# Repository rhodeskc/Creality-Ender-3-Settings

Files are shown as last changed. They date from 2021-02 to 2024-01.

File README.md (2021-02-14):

# Creality-Ender-3-Marlin-v20x-Firmware-Settings
Marlin settings for my Ender 3.

It has the Gulfcoast Robotics heated bed installed, so the temp sensor bed needed to be updated.  In addition to this, I swapped out the board for the 4.2.7 Silent board.

## Creality-Ender-3-board-v4.2.7
Marlin Firmware to get Creality v4.2.7 boards working

Download bugfix from git hub https://github.com/MarlinFirmware/Marlin/archive/bugfix-2.0.x.zip

Download Configuration exemples: https://github.com/MarlinFirmware/Configurations/archive/bugfix-2.0.x.zip

Editing the configuration and building it in Visual Studio Code:
http://813studios.com/creality-4-2-7-marlin-bltouch-install-notes-ender-3/

Instructions on updating and installing the Gulfcoats heated bed: https://letsprint3d.net/how-to-install-the-gulfcoast-robotics-heated-bed-ender-3-5/
* NEW: #define TEMP_SENSOR_BED 11
* OLD: #define TEMP_SENSOR_BED 1

Copy the \_Bootscreen.h and \_Statusscreen.h files to the Marlin\ folder, the same one that has Marlin.ino in it.

## In platformio.ini
* Change:   default_envs = mega2560\
* To:       default_envs = STM32F103RET6_creality

## Compile

In Auto Build Marlin at Visual Studio, click on Build botton and wait for the green line

## Where is the firmware I've compilled
In my case: $\.pio\build\STM32F103RET6_creality\
File to copy to a SD card to flash the firmware: **$\.pio\build\STM32F103RET6_creality\\\*.bin**

## Originally adapted from:
https://github.com/Flawioo/Creality-Ender-3-board-v4.2.7/blob/master/README.md

----

Copied from: http://813studios.com/creality-4-2-7-marlin-bltouch-install-notes-ender-3/

# Creality 4.2.7 Marlin + BLTouch Install notes (Ender-3)

I ordered an upgraded creality v1.1.5 mainboard off Amazon and was shipped Creality’s latest “silent motherboard” version v4.2.7. The product on amazon was described to have a bootloader flashed directly out of box which would make uploading sketches to the board even easier. I spent hours on Arduino IDE trying to upload with the Sanguino board to no avail. 

**Turns out that the new motherboards use the SD card to flash new firmware. All you need to do is drop the “.bin” file to the root directory.**

This made me realize that I just needed to use Visual Studio Code + Auto Build Marlin to compile and update the printer. If you don’t know how to do that, don’t worry– I got you.

Most of this information was found here, these guys got everything working and were able to put together this helpful document that lays out all of the pin data we have so far for the 4.2.7

## Instructions:
Open up VSC and install Auto Build Marlin plugin.

Once you have those both installed, its time to download and open the firmware for the printer inside of Visual Studio Code. 

### Marlin Configuration
First, download the Marlin 2.X.X bugfix from Github here: https://github.com/MarlinFirmware/Marlin/tree/bugfix-2.0.x

Once that’s downloaded, the next step is to open the “Marlin” **folder** that is found inside of the 2.X.X parent directory.

Once you have that opened, now its time to edit the Marlin config files. Below are the changes that I needed make to get my printer working. Take note that this might not necessarily represent your printers setup. 

* Platform.ini
* Configuration.h
* *(optional) Configuration_adv.h*

### Uploading Firmware to the Printer
Once you’ve made all of the changes listed above, compile the firmware with VSC using the Auto Build Marlin plugin and upload it to the root dir of your SD card. Pop the SD card into your printer and boot it up!

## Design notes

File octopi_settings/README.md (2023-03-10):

# Installation Instructions
1. [Install Pi imager for windows](https://www.raspberrypi.com/software/)
1. Run the installer.
1. Configure it per the instructions [here](https://octoprint.org/download/).
1. Open advanced options by clicking on the button with the gear, or by using the keyboard shortcut ctrl+shift+x
> Specific settings used are:
> - OS =  "Choose OS" > "Other Specific Purpose OS" > "3D printing" > "OctoPi" > "stable" version.
> - SSID / WiFi stuff
> - Change password only
1. Click save
1. Flash the card.
1. Install the card back into the Raspberry Pi and let it boot up.
1. Verify by going to [router main settings](http://192.168.1.1) that it has connected to the network
1. Install the following 3rd party plugins
> - [Automatic Shutdown](https://www.reddit.com/r/octoprint/comments/mm9cbi/automatic_shutdown_after_prints/)
> > Got it working. Installed the plugin shutdown printer https://github.com/devildant/OctoPrint-ShutdownPrinter and set that at 110 degrees and at "Extra command / script" put the line "sudo shutdown -h now". Now the rpi turns off at 110 degrees and turns off the relay connected to the printer.
> - [DisplayLayerProgress](https://all3dp.com/2/must-have-octoprint-plugins/)
> - **Do not install ArcWelder**. See notes under [Cura](#Cura).

OctoPi settings were saved at last install. They can be uploaded from *octoprint-backup-latest.zip*

Once that has completed, set the printer profile settings as follows:
> - **Form factor:** Rectangular
> - **Origin:** Lower Left
> - **Heated Bed:** Yes (checked)
> - **Heated Chamber:** No (unchecked)
> - **Width:** 220mm
> - **Depth:** 220mm
> - **Height:** 250mm
> - **Axes:** Default**
> - **Custom Bounding Box:** No (unchecked)
> - **Nozzle Diameter:** 0.4mm
> - **Number of Extruders:** 1

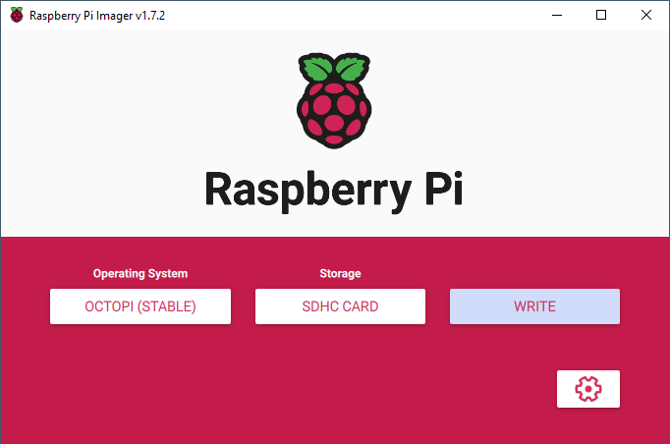
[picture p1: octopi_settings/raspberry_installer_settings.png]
Raspberry Pi settings


## Calibration scripts
1. Create a folder called Calibration
1. Upload calibration scripts from the *\calibration_scripts* directory 

## Cura
1. Install ArcWelder in Cura, but NOT in OctoPrint. It generates a bunch of additional files that are not helpful when you do the OctoPi one.
1. Also install TabAntiWarping extension

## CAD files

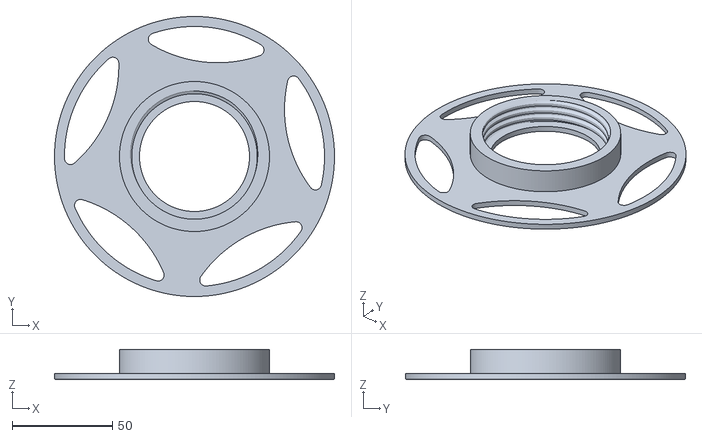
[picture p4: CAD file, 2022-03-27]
calibration_scripts/STLs/MiniSpool_Body2.stl
140.0 x 140.0 x 15.0

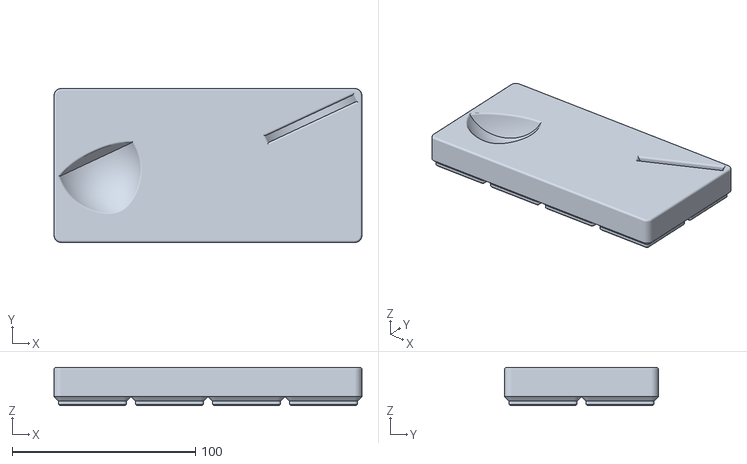
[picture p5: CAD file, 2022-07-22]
common_stl_templates/Gridfinity_Mine/Gridfinity Grinder handle holder.stl
168.0 x 84.0 x 21.0

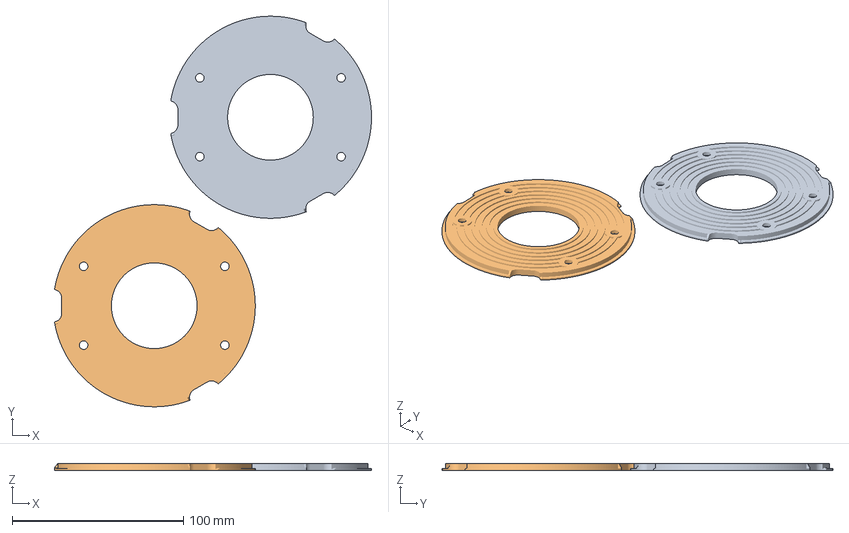
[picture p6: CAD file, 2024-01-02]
common_stl_templates/Simon Nest Backplate.3mf
185.1 x 228.1 x 4.00 mm
Simon Nest Backplate.stl
Simon Nest Backplate.stl 1

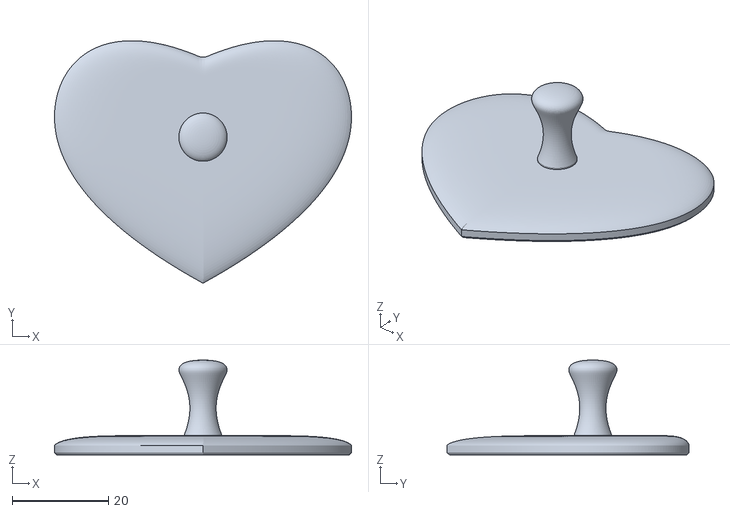
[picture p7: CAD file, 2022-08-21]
creality_supplied_usb/4.Model/box3/HSB2_Lid.stl
61.6 x 50.3 x 19.7

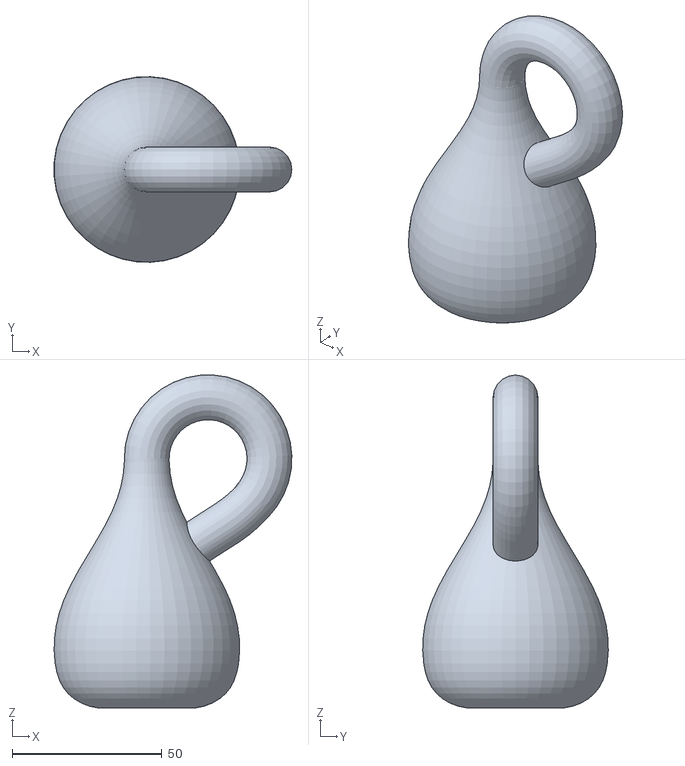
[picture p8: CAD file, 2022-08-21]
creality_supplied_usb/4.Model/Klein bottle.stl
79.4 x 62.0 x 111.2

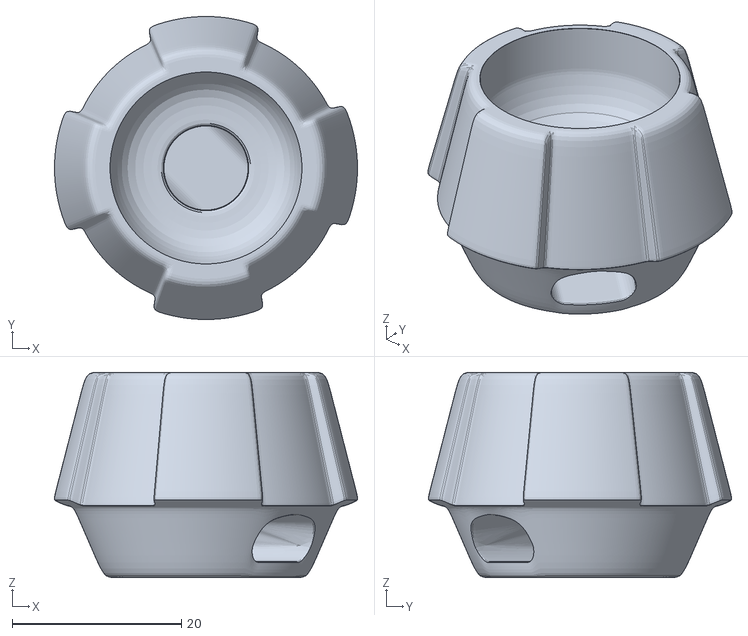
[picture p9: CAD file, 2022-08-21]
creality_supplied_usb/4.Model/quake/Pommel.stl
35.8 x 35.8 x 24.2

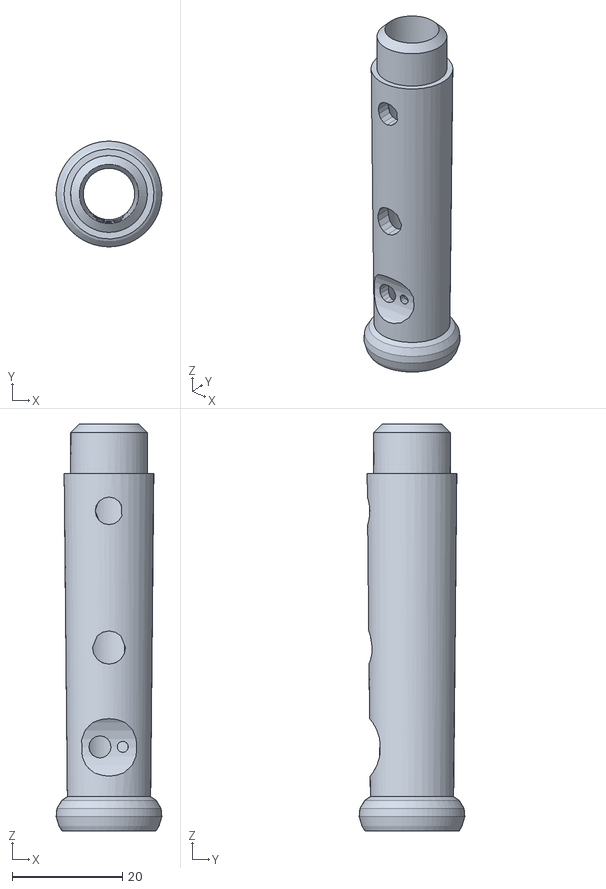
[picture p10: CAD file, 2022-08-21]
creality_supplied_usb/4.Model/recorder/recorderv2.2bodylower.stl
19.1 x 19.1 x 73.7

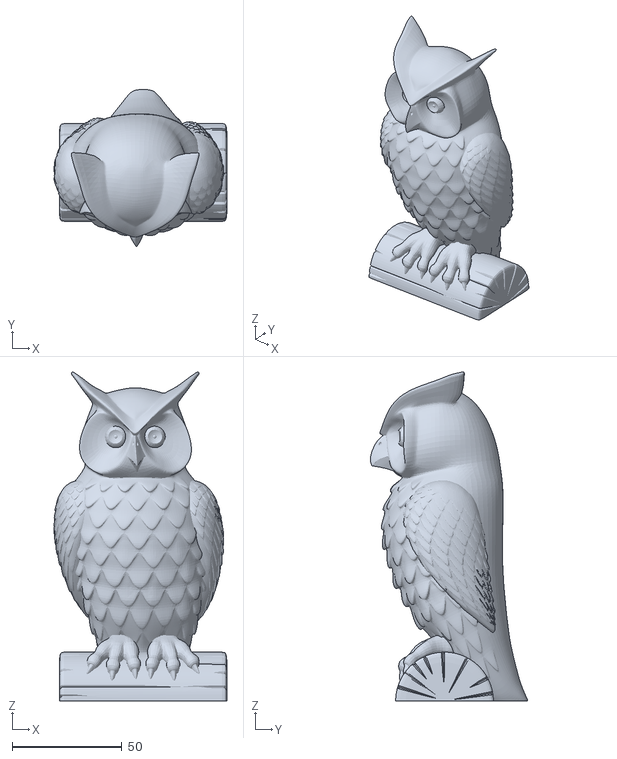
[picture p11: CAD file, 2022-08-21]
creality_supplied_usb/4.Model/the owl/ofw_face_front.STL
78.8 x 71.7 x 150.0

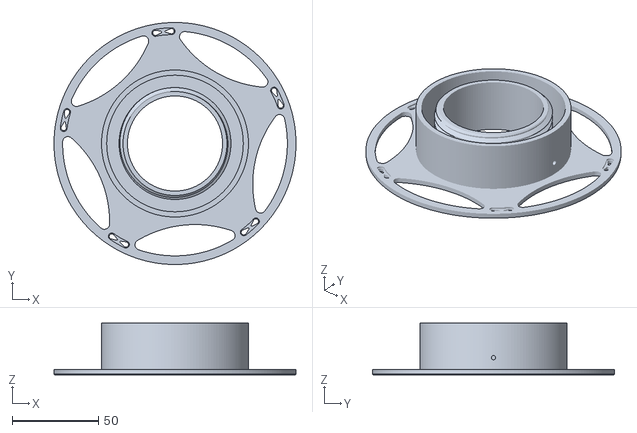
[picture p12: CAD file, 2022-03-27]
calibration_scripts/STLs/MiniSpool_Body1.stl
140.0 x 140.0 x 30.0

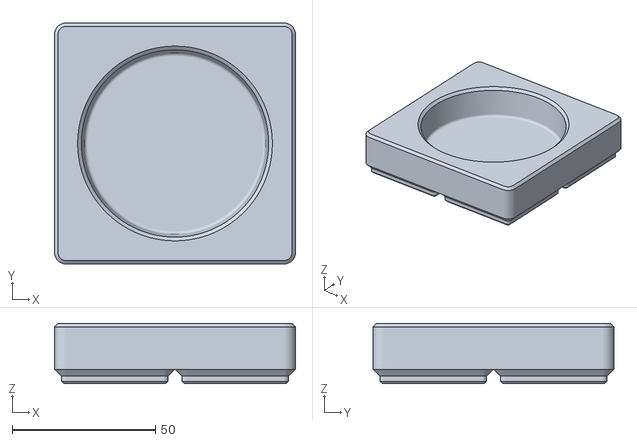
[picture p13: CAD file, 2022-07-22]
common_stl_templates/Gridfinity_Mine/Grinder Bottle Holder.stl
84.0 x 84.0 x 21.0

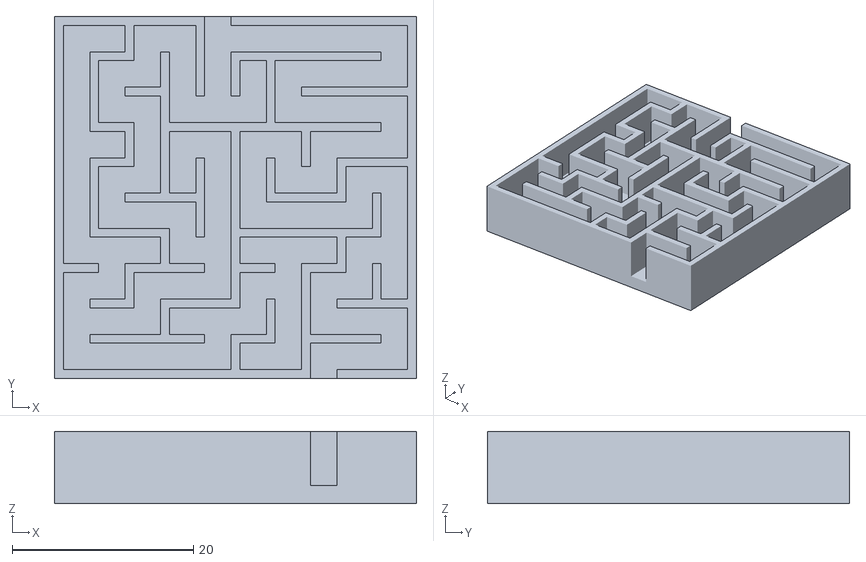
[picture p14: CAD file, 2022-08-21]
creality_supplied_usb/4.Model/maze-10x10.stl
40.0 x 40.0 x 8.00

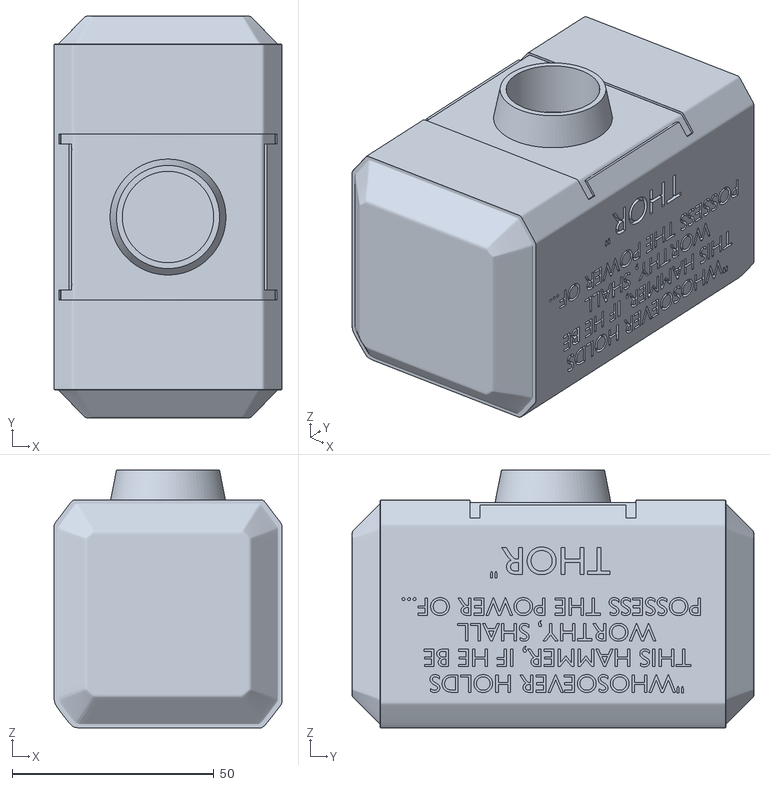
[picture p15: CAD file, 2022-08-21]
creality_supplied_usb/4.Model/quake/Head.stl
56.5 x 99.5 x 63.9

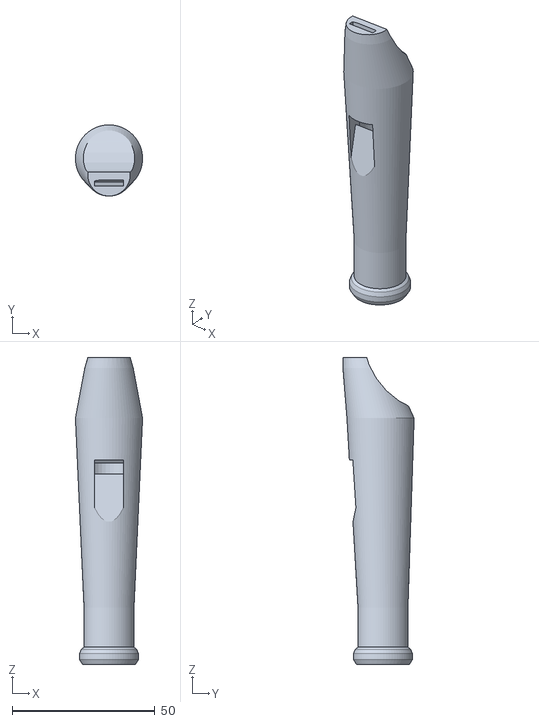
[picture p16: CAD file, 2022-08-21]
creality_supplied_usb/4.Model/recorder/recorderv2.2mouthpiece.stl
23.5 x 24.9 x 107.4

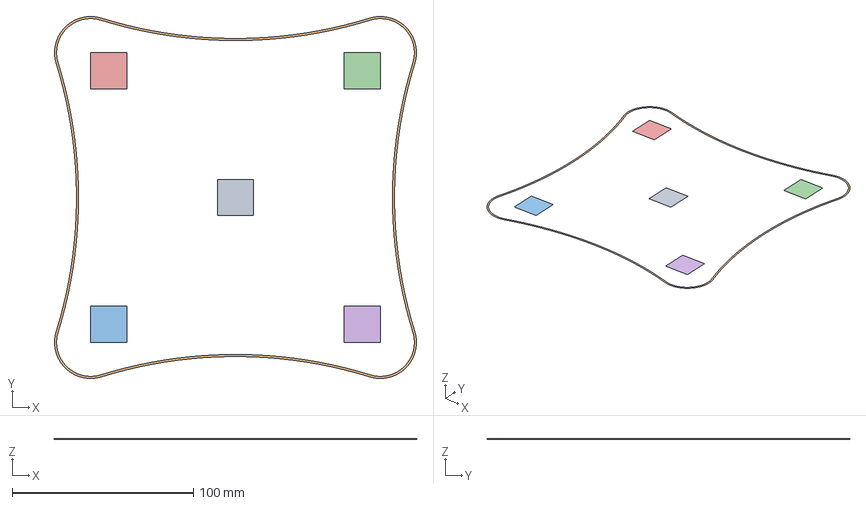
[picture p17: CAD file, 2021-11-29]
calibration_scripts/STLs/Custom Bed Level Test.3mf
200.0 x 200.0 x 0.2 mm

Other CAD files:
common_stl_templates/Gridfinity_Mine/Grinder Box Holder.stl
creality_supplied_usb/4.Model/quake/Hilt.stl
creality_supplied_usb/4.Model/recorder/recorderv2.2.stl
creality_supplied_usb/4.Model/vase.STL
calibration_scripts/STLs/20mm_Calibration_Cube.3mf
calibration_scripts/STLs/20mm_Calibration_Cube.stl
calibration_scripts/STLs/filament_clip_v8.stl
common_stl_templates/Gridfinity_Mine/Grinder Holder.stl
common_stl_templates/Simon Nest Backplate.stl
creality_supplied_usb/4.Model/maze-8x8.stl
creality_supplied_usb/4.Model/recorder/recorderv2.2bodyupper.stl
creality_supplied_usb/4.Model/recorder/recorderv2.2foot.stl
creality_supplied_usb/4.Model/recorder/recorderv2.blend

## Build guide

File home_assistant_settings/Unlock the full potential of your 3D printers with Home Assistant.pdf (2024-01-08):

Unlock the full potential of your 3D printers with Home Assistant. Transform your old Raspberry Pi (RPI) into a powerful tool for monitoring and controlling your 3D Printer(s). Follow the link below to discover the possibilities.
Requirements RPI 3B or higher.
SD card application class 2, 32GB or higher.
Installing HA on your RPI
https://www.home-assistant.io/installation/raspberrypi/
Make a dashboard (give it your printer name or Icon whatever you like) https://www.youtube.com/watch?v=oo2HR6FyV6k
Leave the dashboard empty for the moment you will fill it later.

Once your HA is up and running install HACS (Home Assistant Community Store) Installing HACS
https://www.youtube.com/watch?v=Q8Gj0LiklRE
Install the Bambu Lab integration.
From HACS search for Bambu Lab – click the integration – on this page click the button as shown below

This will install the integration. This will only download the integration and prepare for configuration Activate Bambu Lab integration
In the side menu bar click Settings and then click Devices and services

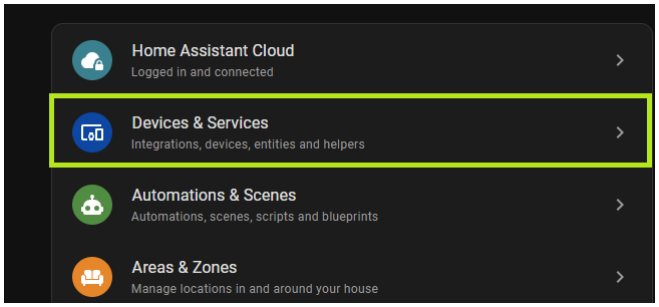
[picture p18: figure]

In the bottom right you will find this button (click the button)

From the following screen select the Bambu Lab integration

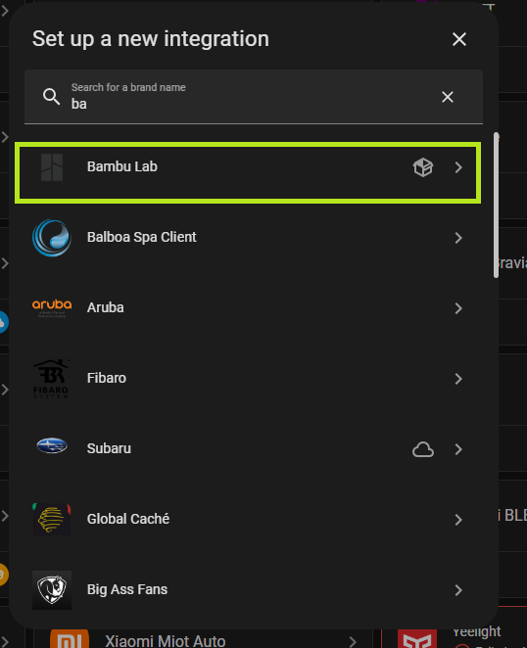
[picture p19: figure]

On the next screen select your printer and connection, I have chosen Bambu Cloud MQTT Have your serial number of the printer ready and make sure your printer is ON.

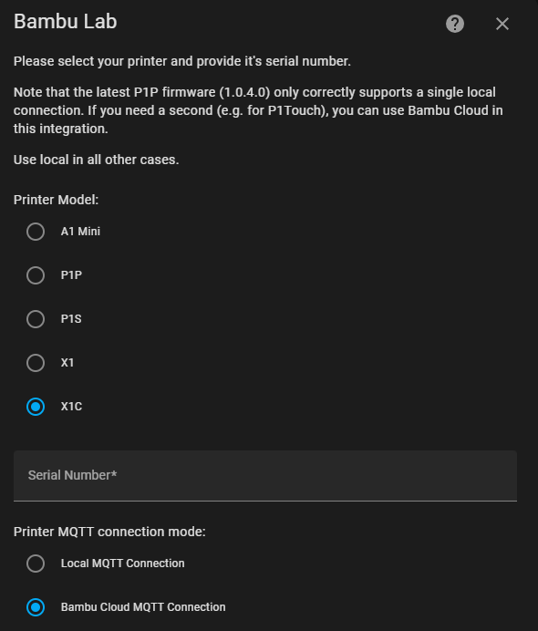
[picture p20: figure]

After this the Integration will be active and you will be presented with a page showing all available sensors and knobs.
You can now send the card to your earlier made dashboard and let the fun begin.
In my video you see some animated icons (FAN)
The are mushroom cards.
I will explain later how you can make these cards

Go to your printer dashboard by selecying Overview and then on the top press the icon or printer name

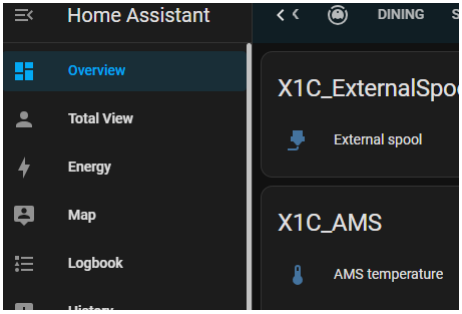
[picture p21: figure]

You can start customizing your dashboard by creating a new card Click in the top right corner the 3 dots – Edit dashboard

In the bottom right click

Now you get following screen

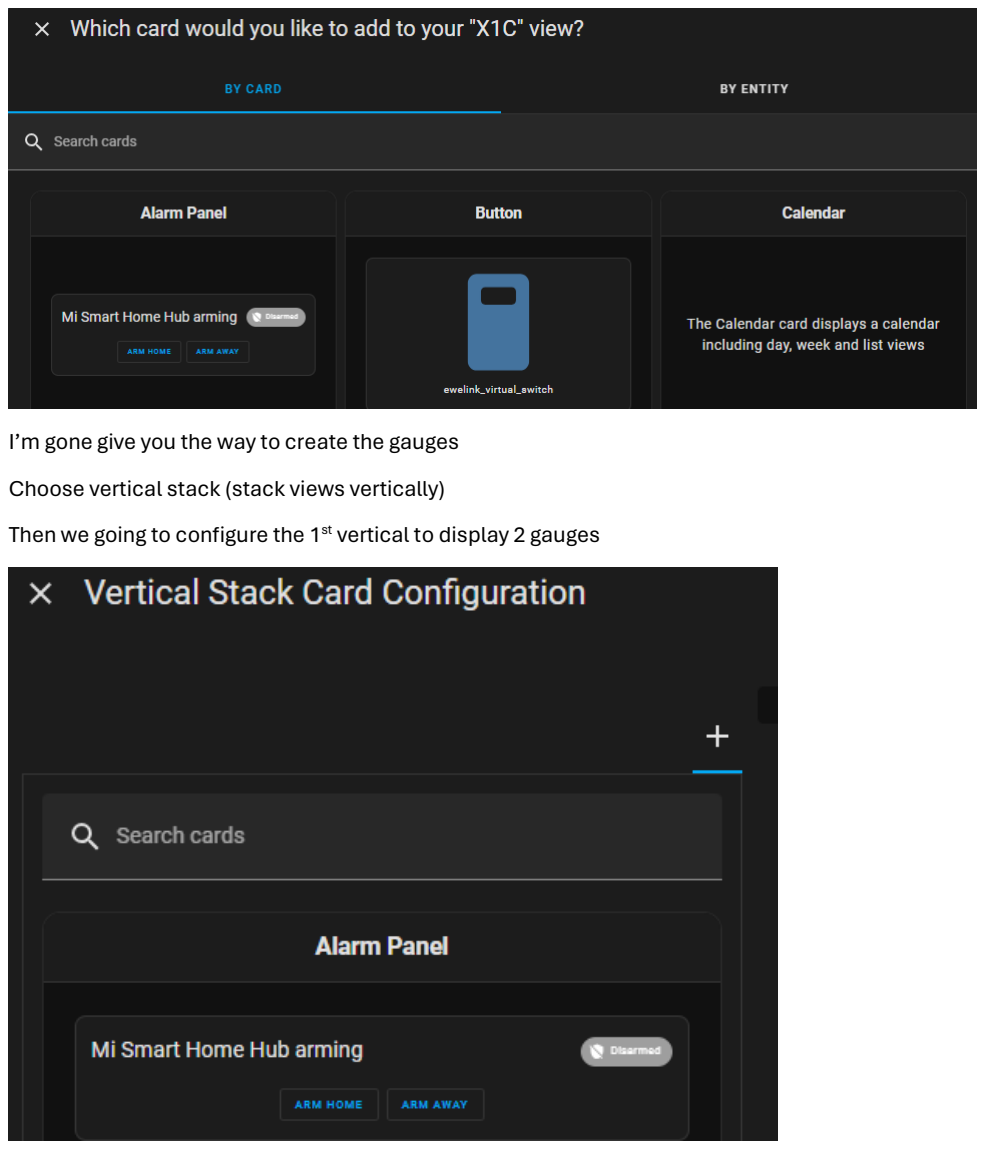
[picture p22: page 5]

I’m gone give you the way to create the gauges
Choose vertical stack (stack views vertically)
Then we going to configure the 1st vertical to display 2 gauges

To do this choose a Horizontal Stack

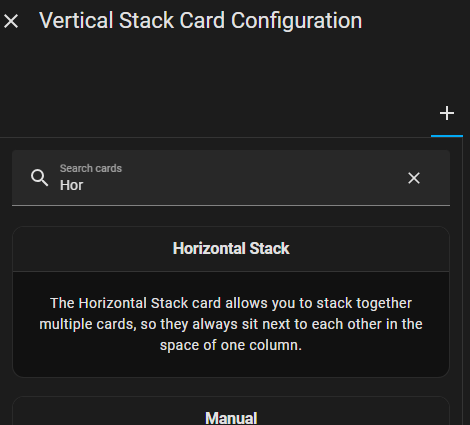
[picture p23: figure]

Then look for Gauge (just type in the search box)

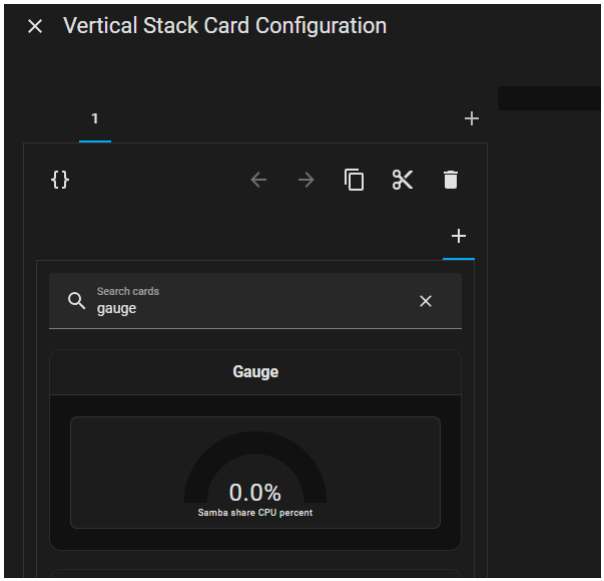
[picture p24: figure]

Select the Gauge and under entity start typing X1C (if you have this type of printer)
It will show you the selection of all available Entities that are available.
Choose for example the nozzle temperature
Under name give it a friendly name example Nozzle and see the picture to configure the other settings. (I removed my serial number)
DON’T PRESS SAVE YET! And wait pressing the + sign

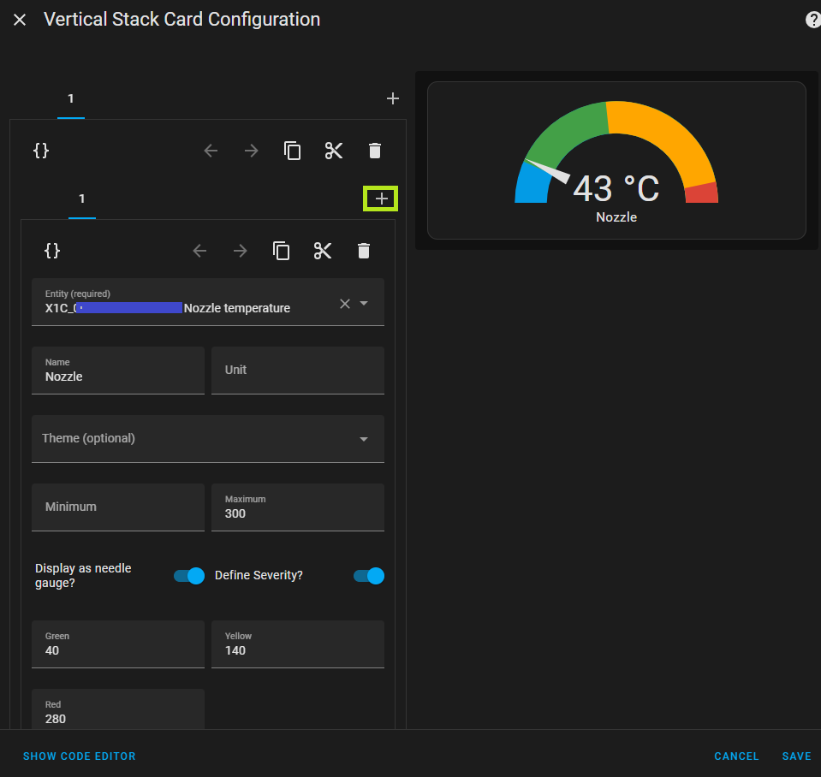
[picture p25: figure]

Now press the + sign as indicated to create your next gauge

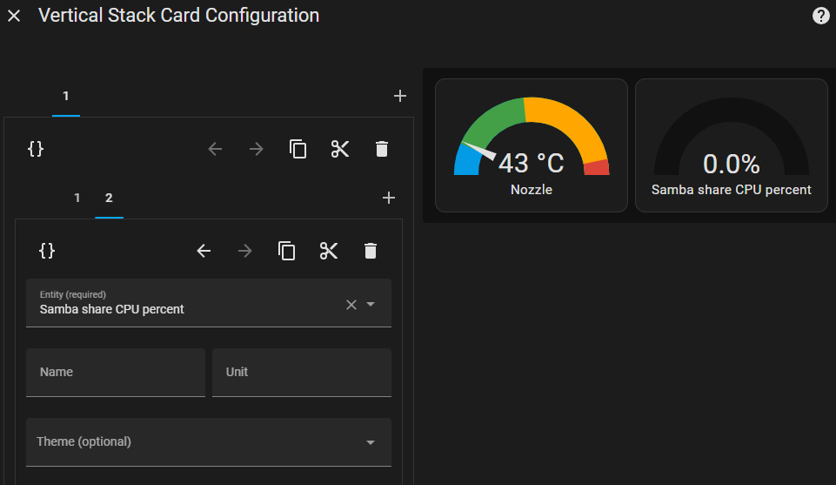
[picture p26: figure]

Repeat and configure your card
Now you can press save of continue with configuring your card
When your done press DONE in the EDIT UI header on the top of your page.You can always come back and press the 3 dots -> edit dashboard and the in the card press the EDIT button.
The animated fan is created with Mushroom cards, if they are not present go to HACS and ad the repository. (Mushroom card)

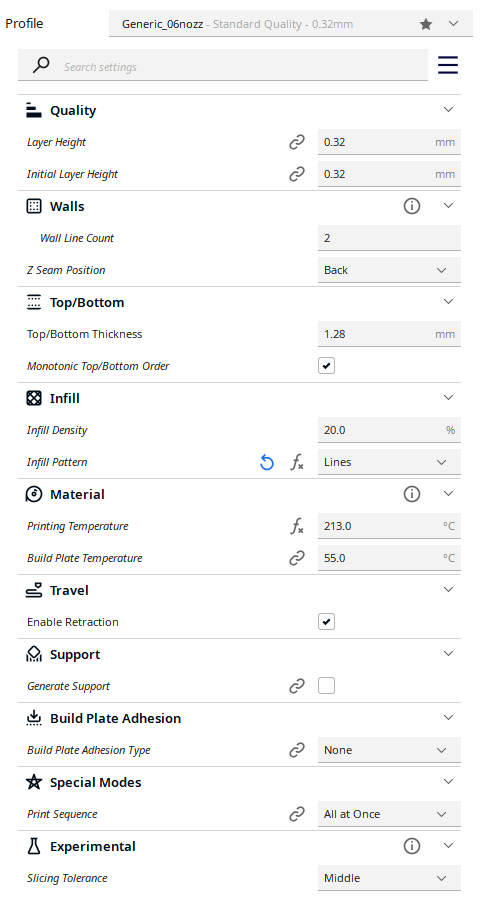
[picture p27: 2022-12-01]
cura_settings/Machine setup/Cura Settings Visibility.png

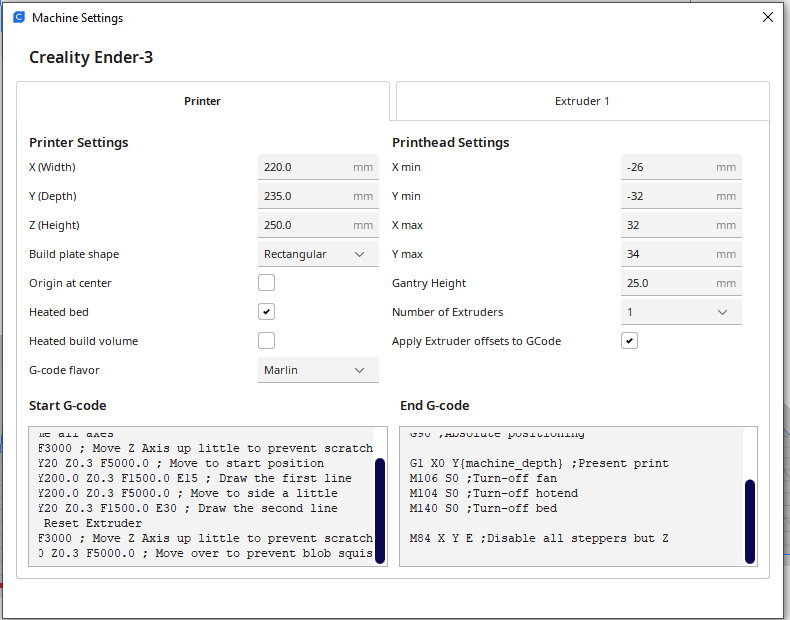
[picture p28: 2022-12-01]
cura_settings/Machine setup/Cura Machine Settings.png

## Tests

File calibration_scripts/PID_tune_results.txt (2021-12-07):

Latest PID tune settings
Old 7/12 6:26p: M301 P24.10 I2.04 D70.99 old

New: M303 E0 S215 C10 U1; // 215C for GST3D black filament
Recv: PID Autotune finished! Put the last Kp, Ki and Kd constants from below into Configuration.h
Recv: #define DEFAULT_Kp 24.88
Recv: #define DEFAULT_Ki 2.28
Recv: #define DEFAULT_Kd 67.81
M301 P24.88 I2.28 D67.81

New: M303 E0 S215 C10 U1; // 215C for GST3D white filament
Recv: PID Autotune finished! Put the last Kp, Ki and Kd constants from below into Configuration.h
Recv: #define DEFAULT_Kp 25.29
Recv: #define DEFAULT_Ki 2.43
Recv: #define DEFAULT_Kd 65.89
M301 P25.29 I2.43 D65.89

New: M303 E0 S200 C10 U1; // 200C for GST3D black filament
Recv:  Classic PID
Recv:  Kp: 26.32 Ki: 2.43 Kd: 71.20
Recv: PID Autotune finished! Put the last Kp, Ki and Kd constants from below into Configuration.h
Recv: #define DEFAULT_Kp 26.32
Recv: #define DEFAULT_Ki 2.43
Recv: #define DEFAULT_Kd 71.20
M301 P26.32 I2.43 D71.20

Hatchbox white:
M301 P24.59 I2.34 D64.55

After each one always:
M500
M503

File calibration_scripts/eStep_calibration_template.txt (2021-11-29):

; Change S215 to whatever the filament should be using here for temperature.

M503 ; get all values and verify. Look at for the calculations: https://github.com/rhodeskc/Creality-Ender-3-Settings/blob/main/Marlin/Configuration.h#L771

; Before performing this step, mark off 20mm and 120mm of filament from a calibration point.
G28 ; Home all axes
G1 Z2.0 F300 ; Move Z Axis up little to prevent scratching of Heat Bed
G1 X100 Y100 Z50 F500.0 ; Move to start position
M82 ;absolute extrusion mode
G92 E0 ; Reset Extruder
M104 S215 ; Hotend to 215
M105 ; Display temperature
M109 S215 ; Wait for hotend to hit 215
G1 F50 ; Set to 50mm per minute, theoretically will be 4 minutes.
G1 E100 F50; Extrude 100mm @ 50mm per minute
M106 S0 ;Turn-off fan
M104 S0 ;Turn-off hotend
M140 S0 ;Turn-off bed
M105 ; Display temperature
M84 X Y E ;Disable all steppers but Z

M503 ; Recv: echo: M92 X80.00 Y80.00 Z400.00 E139.90

M92 E140.9
M500 ; Save settings
M503 ; Report values

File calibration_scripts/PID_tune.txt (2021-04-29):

M503; Get settings before starting test (save for later)
M106; Set blower to 100%
M303 E0 S215 C10 U1; // Hotend, omit U to not save settings
M106 S0; // Turn off blower
M500; Save settings
M503; Read back settings

; ------

; Set hotend settings: M301 P24.10 I2.04 D70.99
; Bed Tune: doesn't work on mine M303 E-1 S60 C10 U1

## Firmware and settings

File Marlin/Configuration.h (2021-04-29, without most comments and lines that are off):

#pragma once
#define CONFIG_EXAMPLES_DIR "Creality/Ender-3/CrealityV427"
#define CONFIGURATION_H_VERSION 020008
#define STRING_CONFIG_H_AUTHOR "(Dust, Ender-3)" // Who made the changes.
#define SHOW_BOOTSCREEN
#define SHOW_CUSTOM_BOOTSCREEN
#define CUSTOM_STATUS_SCREEN_IMAGE
#define SERIAL_PORT 1
#define BAUDRATE 115200
  #define MOTHERBOARD BOARD_CREALITY_V427
#define CUSTOM_MACHINE_NAME "Ender-3 4.2.7"
#define EXTRUDERS 1
#define DEFAULT_NOMINAL_FILAMENT_DIA 1.75
#define TEMP_SENSOR_0 1
#define TEMP_SENSOR_1 0
#define TEMP_SENSOR_2 0
#define TEMP_SENSOR_3 0
#define TEMP_SENSOR_4 0
#define TEMP_SENSOR_5 0
#define TEMP_SENSOR_6 0
#define TEMP_SENSOR_7 0
#define TEMP_SENSOR_BED 11
#define TEMP_SENSOR_PROBE 0
#define TEMP_SENSOR_CHAMBER 0
#define DUMMY_THERMISTOR_998_VALUE  25
#define DUMMY_THERMISTOR_999_VALUE 100
#define MAX_REDUNDANT_TEMP_SENSOR_DIFF 10
#define TEMP_RESIDENCY_TIME     10  // (seconds) Time to wait for hotend to "settle" in M109
#define TEMP_WINDOW              1  // (°C) Temperature proximity for the "temperature reached" timer
#define TEMP_HYSTERESIS          3  // (°C) Temperature proximity considered "close enough" to the target
#define TEMP_BED_RESIDENCY_TIME 10  // (seconds) Time to wait for bed to "settle" in M190
#define TEMP_BED_WINDOW          1  // (°C) Temperature proximity for the "temperature reached" timer
#define TEMP_BED_HYSTERESIS      3  // (°C) Temperature proximity considered "close enough" to the target
#define HEATER_0_MINTEMP   5
#define HEATER_1_MINTEMP   5
#define HEATER_2_MINTEMP   5
#define HEATER_3_MINTEMP   5
#define HEATER_4_MINTEMP   5
#define HEATER_5_MINTEMP   5
#define HEATER_6_MINTEMP   5
#define HEATER_7_MINTEMP   5
#define BED_MINTEMP        5
#define HEATER_0_MAXTEMP 275
#define HEATER_1_MAXTEMP 275
#define HEATER_2_MAXTEMP 275
#define HEATER_3_MAXTEMP 275
#define HEATER_4_MAXTEMP 275
#define HEATER_5_MAXTEMP 275
#define HEATER_6_MAXTEMP 275
#define HEATER_7_MAXTEMP 275
#define BED_MAXTEMP      125
#define PIDTEMP
#define BANG_MAX 255     // Limits current to nozzle while in bang-bang mode; 255=full current
#define PID_MAX BANG_MAX // Limits current to nozzle while PID is active (see PID_FUNCTIONAL_RANGE below); 255=full current
#define PID_K1 0.95      // Smoothing factor within any PID loop
  #define PID_EDIT_MENU           // Add PID editing to the "Advanced Settings" menu. (~700 bytes of PROGMEM)
  #define PID_AUTOTUNE_MENU       // Add PID auto-tuning to the "Advanced Settings" menu. (~250 bytes of PROGMEM)
    #define DEFAULT_Kp  24.10
    #define DEFAULT_Ki   2.04
    #define DEFAULT_Kd  70.99
#define MAX_BED_POWER 255 // limits duty cycle to bed; 255=full current
  #define PID_FUNCTIONAL_RANGE 10 // If the temperature difference between the target temperature and the actual temperature
#define PREVENT_COLD_EXTRUSION
#define EXTRUDE_MINTEMP 170
#define PREVENT_LENGTHY_EXTRUDE
#define EXTRUDE_MAXLENGTH 200
#define THERMAL_PROTECTION_HOTENDS // Enable thermal protection for all extruders
#define THERMAL_PROTECTION_BED     // Enable thermal protection for the heated bed
#define THERMAL_PROTECTION_CHAMBER // Enable thermal protection for the heated chamber
#define USE_XMIN_PLUG
#define USE_YMIN_PLUG
#define USE_ZMIN_PLUG
#define ENDSTOPPULLUPS
#define X_MIN_ENDSTOP_INVERTING false // Set to true to invert the logic of the endstop.
#define Y_MIN_ENDSTOP_INVERTING false // Set to true to invert the logic of the endstop.
#define Z_MIN_ENDSTOP_INVERTING false // Set to true to invert the logic of the endstop.
#define X_MAX_ENDSTOP_INVERTING false // Set to true to invert the logic of the endstop.
#define Y_MAX_ENDSTOP_INVERTING false // Set to true to invert the logic of the endstop.
#define Z_MAX_ENDSTOP_INVERTING false // Set to true to invert the logic of the endstop.
#define Z_MIN_PROBE_ENDSTOP_INVERTING false // Set to true to invert the logic of the probe.
#define X_DRIVER_TYPE  TMC2208_STANDALONE
#define Y_DRIVER_TYPE  TMC2208_STANDALONE
#define Z_DRIVER_TYPE  TMC2208_STANDALONE
#define E0_DRIVER_TYPE TMC2208_STANDALONE
#define DEFAULT_AXIS_STEPS_PER_UNIT   { 80, 80, 400, 139.9 }
#define DEFAULT_MAX_FEEDRATE          { 500, 500, 5, 25 }
#define DEFAULT_MAX_ACCELERATION      { 500, 500, 100, 5000 }
#define DEFAULT_ACCELERATION          500    // X, Y, Z and E acceleration for printing moves
#define DEFAULT_RETRACT_ACCELERATION  500    // E acceleration for retracts
#define DEFAULT_TRAVEL_ACCELERATION   500    // X, Y, Z acceleration for travel (non printing) moves
#define DEFAULT_EJERK    5.0  // May be used by Linear Advance
  #define JUNCTION_DEVIATION_MM 0.08  // (mm) Distance from real junction edge
  #define JD_HANDLE_SMALL_SEGMENTS    // Use curvature estimation instead of just the junction angle
#define Z_MIN_PROBE_USES_Z_MIN_ENDSTOP_PIN
#define NOZZLE_TO_PROBE_OFFSET { 10, 10, 0 }
#define PROBING_MARGIN 10
#define XY_PROBE_SPEED (133*60)
#define Z_PROBE_SPEED_FAST (4*60)
#define Z_PROBE_SPEED_SLOW (Z_PROBE_SPEED_FAST / 2)
#define Z_CLEARANCE_DEPLOY_PROBE   10 // Z Clearance for Deploy/Stow
#define Z_CLEARANCE_BETWEEN_PROBES  5 // Z Clearance between probe points
#define Z_CLEARANCE_MULTI_PROBE     5 // Z Clearance between multiple probes
#define Z_PROBE_LOW_POINT          -2 // Farthest distance below the trigger-point to go before stopping
#define Z_PROBE_OFFSET_RANGE_MIN -20
#define Z_PROBE_OFFSET_RANGE_MAX 20
#define X_ENABLE_ON 0
#define Y_ENABLE_ON 0
#define Z_ENABLE_ON 0
#define E_ENABLE_ON 0 // For all extruders
#define DISABLE_X false
#define DISABLE_Y false
#define DISABLE_Z false
#define DISABLE_E false             // Disable the extruder when not stepping
#define INVERT_X_DIR false
#define INVERT_Y_DIR false
#define INVERT_Z_DIR true
#define INVERT_E0_DIR false
#define INVERT_E1_DIR false
#define INVERT_E2_DIR false
#define INVERT_E3_DIR false
#define INVERT_E4_DIR false
#define INVERT_E5_DIR false
#define INVERT_E6_DIR false
#define INVERT_E7_DIR false
#define X_HOME_DIR -1
#define Y_HOME_DIR -1
#define Z_HOME_DIR -1
#define X_BED_SIZE 235
#define Y_BED_SIZE 235
#define X_MIN_POS -5
#define Y_MIN_POS -10
#define Z_MIN_POS 0
#define X_MAX_POS X_BED_SIZE
#define Y_MAX_POS Y_BED_SIZE
#define Z_MAX_POS 250
#define MIN_SOFTWARE_ENDSTOPS
  #define MIN_SOFTWARE_ENDSTOP_X
  #define MIN_SOFTWARE_ENDSTOP_Y
  #define MIN_SOFTWARE_ENDSTOP_Z
#define MAX_SOFTWARE_ENDSTOPS
  #define MAX_SOFTWARE_ENDSTOP_X
  #define MAX_SOFTWARE_ENDSTOP_Y
  #define MAX_SOFTWARE_ENDSTOP_Z
#define HOMING_FEEDRATE_MM_M { (20*60), (20*60), (4*60) }
#define VALIDATE_HOMING_ENDSTOPS
#define EEPROM_SETTINGS       // Persistent storage with M500 and M501
#define EEPROM_CHITCHAT       // Give feedback on EEPROM commands. Disable to save PROGMEM.
#define EEPROM_BOOT_SILENT    // Keep M503 quiet and only give errors during first load
#define HOST_KEEPALIVE_FEATURE        // Disable this if your host doesn't like keepalive messages
#define DEFAULT_KEEPALIVE_INTERVAL 2  // Number of seconds between "busy" messages. Set with M113.
#define BUSY_WHILE_HEATING            // Some hosts require "busy" messages even during heating
#define PREHEAT_1_LABEL       "PLA"
#define PREHEAT_1_TEMP_HOTEND 185
#define PREHEAT_1_TEMP_BED     45
#define PREHEAT_1_FAN_SPEED   255 // Value from 0 to 255
#define PREHEAT_2_LABEL       "ABS"
#define PREHEAT_2_TEMP_HOTEND 240
#define PREHEAT_2_TEMP_BED     70
#define PREHEAT_2_FAN_SPEED   255 // Value from 0 to 255
#define PRINTJOB_TIMER_AUTOSTART
#define LCD_LANGUAGE en
#define DISPLAY_CHARSET_HD44780 JAPANESE
#define LCD_INFO_SCREEN_STYLE 0
#define SDSUPPORT
#define SPEAKER
#define CR10_STOCKDISPLAY
  #define RET6_12864_LCD  // Specific to the SoC (can either be RET / VET)
#define SOFT_PWM_SCALE 0
#define SERVO_DELAY { 300 }

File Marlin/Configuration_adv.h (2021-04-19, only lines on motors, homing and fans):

#define E0_AUTO_FAN_PIN -1
#define E1_AUTO_FAN_PIN -1
#define E2_AUTO_FAN_PIN -1
#define E3_AUTO_FAN_PIN -1
#define E4_AUTO_FAN_PIN -1
#define E5_AUTO_FAN_PIN -1
#define E6_AUTO_FAN_PIN -1
#define E7_AUTO_FAN_PIN -1
#define CHAMBER_AUTO_FAN_PIN -1
#define HOMING_BUMP_MM      { 5, 5, 2 }       // (mm) Backoff from endstops after first bump
#define HOMING_BUMP_DIVISOR { 2, 2, 4 }       // Re-Bump Speed Divisor (Divides the Homing Feedrate)
#define MICROSTEP_MODES { 16, 16, 16, 16, 16, 16 } // [1,2,4,8,16]
#define LIN_ADVANCE
  #define LIN_ADVANCE_K 0.01    // Unit: mm compression per 1mm/s extruder speed

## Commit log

2021-02-02 Initial Ender 3 settings flashed to Marlin board
    [Configuration.h, Configuration_adv.h]
2021-02-26 Updating PID Autotune values.
    [Configuration.h]
2021-02-26 Updating PID Autotune values (fix comments).
    [Configuration.h]
2021-04-04 Enabling Linear Advance K=0.12 for Microswiss Direct Drive
    [Configuration_adv.h]
2021-04-19 Direct Drive update. Changed Extruder steps to 140, set linear advance to k=0.12.
    [Configuration.h]
2021-04-19 Setting X,Y offset to -5,-10
    [Configuration.h]
2021-04-29 Setting E139.90
    [Configuration.h]
2021-04-29 Calibration scripts
2021-04-29 Calibration prints have removed one of the pauses
2021-05-13 Update filament_swap_template.txt
    Changing comments
2021-07-25 Adding "print end" GCode for servicing
2021-07-25 Adding bed level with a M0 pause to adjust temperatures if desired.
2021-09-08 Archiving and moving STLs
    [20mm_Calibration_Cube.3mf, 20mm_Calibration_Cube.stl, filament_clip_v8.stl]
2021-09-08 Create @ Commands — OctoPrint master documentation.url
2021-11-29 Create Custom Bed Level Test.gcode
2021-11-29 Create Custom Bed Level Test.3mf
    [Custom Bed Level Test.3mf]
2022-03-27 20220326 mini spool bodies (#20)
    * Create MiniSpool_Body1.stl
    * Create MiniSpool_Body2.stl
    [MiniSpool_Body1.stl, MiniSpool_Body2.stl]
2022-07-22 Gridfinity (#21)
    * Create Gridfinity Baseplates.zip
    * Create ZackFreedman - 3D model uploads - Thangs.url
    * Create G28_first_4_point_check - z0.gcode
    * My 3D printer bodies
    [Gridfinity Grinder handle holder.stl, Grinder Bottle Holder.stl, Grinder Box Holder.stl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]
2022-07-22 Gridfinity (#22)
    * Create Gridfinity storage boxes by DatBuschi - Download free STL model - Printables.com.url
    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
2022-08-21 Adding creality ender 3 default stuff, NEW imager instructions and plugin readme (#24)
    * Add creality USB stuff
    * Octopi settings v1
    * Update README.md
    * Create octoprint-backup-latest.zip
    * Create Set-LKGBackup.ps1
    * Update Set-LKGBackup.ps1
    [HSB2_Lid.stl, Head.stl, Hilt.stl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]
2022-11-17 Cura profiles for 0.6 nozzle
2023-12-07 Add Simon's Nest alarm backplate
    [Simon Nest Backplate.stl]
2024-01-02 Create Simon Nest Backplate.3mf
    [Simon Nest Backplate.3mf]
2024-01-08 Create Unlock the full potential of your 3D printers with Home Assistant.pdf

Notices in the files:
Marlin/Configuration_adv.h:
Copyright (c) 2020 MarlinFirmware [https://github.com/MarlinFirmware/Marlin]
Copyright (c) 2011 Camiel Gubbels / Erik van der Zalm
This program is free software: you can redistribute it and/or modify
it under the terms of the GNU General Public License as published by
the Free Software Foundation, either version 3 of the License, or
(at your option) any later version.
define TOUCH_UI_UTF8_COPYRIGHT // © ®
